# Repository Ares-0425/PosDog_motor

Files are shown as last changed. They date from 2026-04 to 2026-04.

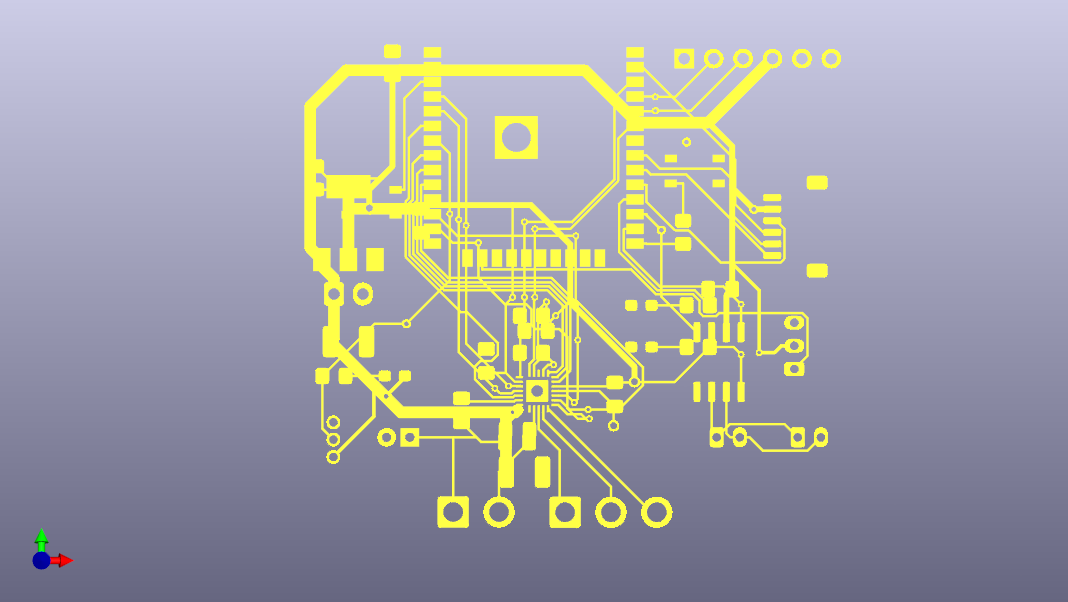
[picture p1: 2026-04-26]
drv8311/drv8311.png

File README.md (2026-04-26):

# PosDog_motor
四脚歩行ロボット「PosDog」のモータードライバプログラムと回路CADデータのレポジトリ
## 動作環境
プログラムはVSCode＋PlatformIO環境で作成しています。
回路CADはKiCADを使用し、JLCPCBでの発注を想定しています。
## ファイル
### プログラム
レポジトリ全体がPlatformIOのプログラムフォルダになっていますが、いじるべきプログラムは"src"フォルダ内に入っています。
- main.cpp  
  メインプログラムファイル。主にSimpleFOC（モーター制御ライブラリ）の設定、SimpleFOC制御ループ、CAN通信で取得した文字列の識別と文字列に応じた動作の実行、キャリブレーション動作の定義、を行っている。
- can.hpp  
  can.cppのヘッダー
- can.cpp  
  can通信用ファイル。設定と受信時のID及び文字列格納。
- dob.hpp  
  dob.cppのヘッダー
- dob.cpp  
  外乱オブザーバーと、外乱オブザーバーを考慮したトルク制御と角度制御の指令値出力。
- identification.hpp  
  identification.cppのヘッダー
- identification.cpp  
  システム同定を一瞬やろうとした時の残骸
### 回路
"drv8311"フォルダ内に入っています。
- drv8311.kicad_pro  
  kicadプロジェクトファイル
- drv8311.kicad_sch  
  kicad回路図ファイル
- drv8311.kicad_pcb  
  kicadPCBファイル
- production
  - drv8311.zip  
    JLCPCB発注用ファイル
## 基本の使いかた
プログラムを書き込む脚に合わせて、main.cppの"#define LEG"の数字を変更する。

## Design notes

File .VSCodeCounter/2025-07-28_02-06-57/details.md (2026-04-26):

# Details

Date : 2025-07-28 02:06:57

Directory e:\\OneDrive\\vscode\\zyudou\\M5-controll

Total : 17 files,  1201 codes, 63 comments, 196 blanks, all 1460 lines

[Summary](results.md) / Details / [Diff Summary](diff.md) / [Diff Details](diff-details.md)

## Files
| filename | language | code | comment | blank | total |
| :--- | :--- | ---: | ---: | ---: | ---: |
| [M5-controll/.VSCodeCounter/2025-07-28\_02-06-30/details.md](/M5-controll/.VSCodeCounter/2025-07-28_02-06-30/details.md) | Markdown | 21 | 0 | 6 | 27 |
| [M5-controll/.VSCodeCounter/2025-07-28\_02-06-30/diff-details.md](/M5-controll/.VSCodeCounter/2025-07-28_02-06-30/diff-details.md) | Markdown | 9 | 0 | 6 | 15 |
| [M5-controll/.VSCodeCounter/2025-07-28\_02-06-30/diff.md](/M5-controll/.VSCodeCounter/2025-07-28_02-06-30/diff.md) | Markdown | 12 | 0 | 7 | 19 |
| [M5-controll/.VSCodeCounter/2025-07-28\_02-06-30/results.json](/M5-controll/.VSCodeCounter/2025-07-28_02-06-30/results.json) | JSON | 1 | 0 | 0 | 1 |
| [M5-controll/.VSCodeCounter/2025-07-28\_02-06-30/results.md](/M5-controll/.VSCodeCounter/2025-07-28_02-06-30/results.md) | Markdown | 17 | 0 | 7 | 24 |
| [M5-controll/platformio.ini](/M5-controll/platformio.ini) | Ini | 21 | 9 | 5 | 35 |
| [M5-controll/src/can.cpp](/M5-controll/src/can.cpp) | C++ | 59 | 6 | 12 | 77 |
| [M5-controll/src/can.hpp](/M5-controll/src/can.hpp) | C++ | 26 | 2 | 5 | 33 |
| [M5-controll/src/control.cpp](/M5-controll/src/control.cpp) | C++ | 803 | 28 | 98 | 929 |
| [M5-controll/src/control.hpp](/M5-controll/src/control.hpp) | C++ | 19 | 2 | 4 | 25 |
| [M5-controll/src/display.cpp](/M5-controll/src/display.cpp) | C++ | 45 | 0 | 6 | 51 |
| [M5-controll/src/display.hpp](/M5-controll/src/display.hpp) | C++ | 11 | 2 | 5 | 18 |
| [M5-controll/src/imu.cpp](/M5-controll/src/imu.cpp) | C++ | 68 | 14 | 23 | 105 |
| [M5-controll/src/imu.hpp](/M5-controll/src/imu.hpp) | C++ | 13 | 0 | 3 | 16 |
| [M5-controll/src/main.cpp](/M5-controll/src/main.cpp) | C++ | 73 | 0 | 7 | 80 |
| [M5-controll/src/sd.cpp](/M5-controll/src/sd.cpp) | C++ | 0 | 0 | 1 | 1 |
| [M5-controll/src/sd.hpp](/M5-controll/src/sd.hpp) | C++ | 3 | 0 | 1 | 4 |

[Summary](results.md) / Details / [Diff Summary](diff.md) / [Diff Details](diff-details.md)

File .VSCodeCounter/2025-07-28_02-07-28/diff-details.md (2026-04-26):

# Diff Details

Date : 2025-07-28 02:07:28

Directory e:\\OneDrive\\vscode\\zyudou\\simpleFOC_CAN_DOB

Total : 28 files,  -482 codes, 169 comments, -19 blanks, all -332 lines

[Summary](results.md) / [Details](details.md) / [Diff Summary](diff.md) / Diff Details

## Files
| filename | language | code | comment | blank | total |
| :--- | :--- | ---: | ---: | ---: | ---: |
| [M5-controll/.VSCodeCounter/2025-07-28\_02-06-30/details.md](/M5-controll/.VSCodeCounter/2025-07-28_02-06-30/details.md) | Markdown | -21 | 0 | -6 | -27 |
| [M5-controll/.VSCodeCounter/2025-07-28\_02-06-30/diff-details.md](/M5-controll/.VSCodeCounter/2025-07-28_02-06-30/diff-details.md) | Markdown | -9 | 0 | -6 | -15 |
| [M5-controll/.VSCodeCounter/2025-07-28\_02-06-30/diff.md](/M5-controll/.VSCodeCounter/2025-07-28_02-06-30/diff.md) | Markdown | -12 | 0 | -7 | -19 |
| [M5-controll/.VSCodeCounter/2025-07-28\_02-06-30/results.json](/M5-controll/.VSCodeCounter/2025-07-28_02-06-30/results.json) | JSON | -1 | 0 | 0 | -1 |
| [M5-controll/.VSCodeCounter/2025-07-28\_02-06-30/results.md](/M5-controll/.VSCodeCounter/2025-07-28_02-06-30/results.md) | Markdown | -17 | 0 | -7 | -24 |
| [M5-controll/platformio.ini](/M5-controll/platformio.ini) | Ini | -21 | -9 | -5 | -35 |
| [M5-controll/src/can.cpp](/M5-controll/src/can.cpp) | C++ | -59 | -6 | -12 | -77 |
| [M5-controll/src/can.hpp](/M5-controll/src/can.hpp) | C++ | -26 | -2 | -5 | -33 |
| [M5-controll/src/control.cpp](/M5-controll/src/control.cpp) | C++ | -803 | -28 | -98 | -929 |
| [M5-controll/src/control.hpp](/M5-controll/src/control.hpp) | C++ | -19 | -2 | -4 | -25 |
| [M5-controll/src/display.cpp](/M5-controll/src/display.cpp) | C++ | -45 | 0 | -6 | -51 |
| [M5-controll/src/display.hpp](/M5-controll/src/display.hpp) | C++ | -11 | -2 | -5 | -18 |
| [M5-controll/src/imu.cpp](/M5-controll/src/imu.cpp) | C++ | -68 | -14 | -23 | -105 |
| [M5-controll/src/imu.hpp](/M5-controll/src/imu.hpp) | C++ | -13 | 0 | -3 | -16 |
| [M5-controll/src/main.cpp](/M5-controll/src/main.cpp) | C++ | -73 | 0 | -7 | -80 |
| [M5-controll/src/sd.cpp](/M5-controll/src/sd.cpp) | C++ | 0 | 0 | -1 | -1 |
| [M5-controll/src/sd.hpp](/M5-controll/src/sd.hpp) | C++ | -3 | 0 | -1 | -4 |
| [simpleFOC\_CAN\_DOB/.VSCodeCounter/2025-07-28\_02-06-57/details.md](/simpleFOC_CAN_DOB/.VSCodeCounter/2025-07-28_02-06-57/details.md) | Markdown | 26 | 0 | 6 | 32 |
| [simpleFOC\_CAN\_DOB/.VSCodeCounter/2025-07-28\_02-06-57/diff-details.md](/simpleFOC_CAN_DOB/.VSCodeCounter/2025-07-28_02-06-57/diff-details.md) | Markdown | 9 | 0 | 6 | 15 |
| [simpleFOC\_CAN\_DOB/.VSCodeCounter/2025-07-28\_02-06-57/diff.md](/simpleFOC_CAN_DOB/.VSCodeCounter/2025-07-28_02-06-57/diff.md) | Markdown | 12 | 0 | 7 | 19 |
| [simpleFOC\_CAN\_DOB/.VSCodeCounter/2025-07-28\_02-06-57/results.json](/simpleFOC_CAN_DOB/.VSCodeCounter/2025-07-28_02-06-57/results.json) | JSON | 1 | 0 | 0 | 1 |
| [simpleFOC\_CAN\_DOB/.VSCodeCounter/2025-07-28\_02-06-57/results.md](/simpleFOC_CAN_DOB/.VSCodeCounter/2025-07-28_02-06-57/results.md) | Markdown | 21 | 0 | 7 | 28 |
| [simpleFOC\_CAN\_DOB/platformio.ini](/simpleFOC_CAN_DOB/platformio.ini) | Ini | 12 | 9 | 2 | 23 |
| [simpleFOC\_CAN\_DOB/src/can.cpp](/simpleFOC_CAN_DOB/src/can.cpp) | C++ | 62 | 4 | 14 | 80 |
| [simpleFOC\_CAN\_DOB/src/can.hpp](/simpleFOC_CAN_DOB/src/can.hpp) | C++ | 17 | 2 | 5 | 24 |
| [simpleFOC\_CAN\_DOB/src/dob.cpp](/simpleFOC_CAN_DOB/src/dob.cpp) | C++ | 118 | 51 | 38 | 207 |
| [simpleFOC\_CAN\_DOB/src/dob.hpp](/simpleFOC_CAN_DOB/src/dob.hpp) | C++ | 41 | 7 | 10 | 58 |
| [simpleFOC\_CAN\_DOB/src/main.cpp](/simpleFOC_CAN_DOB/src/main.cpp) | C++ | 400 | 159 | 82 | 641 |

[Summary](results.md) / [Details](details.md) / [Diff Summary](diff.md) / Diff Details

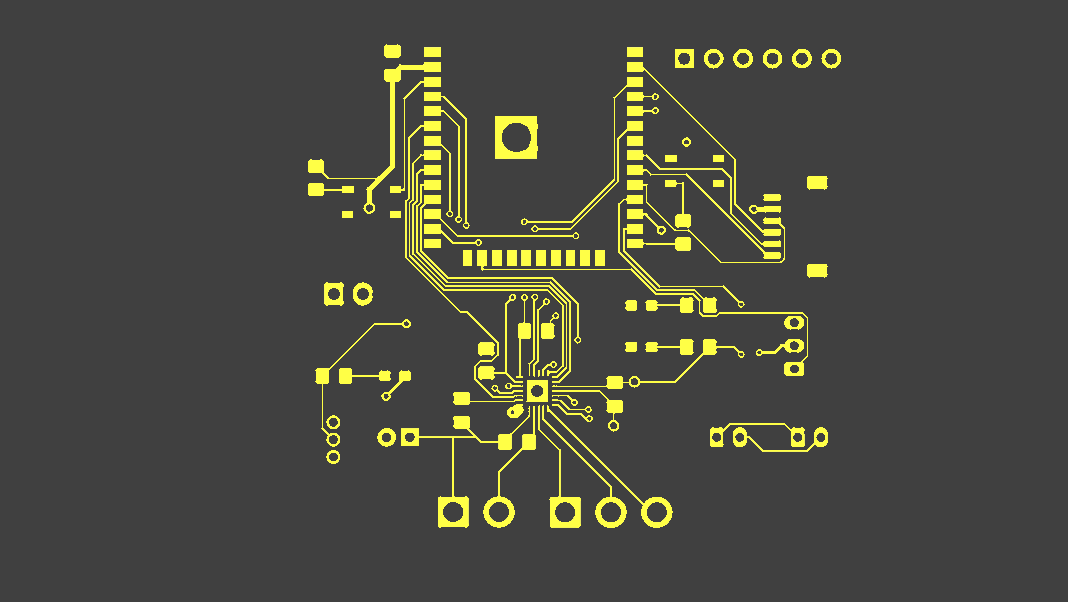
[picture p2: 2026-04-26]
drv8311/drv8311-1.png

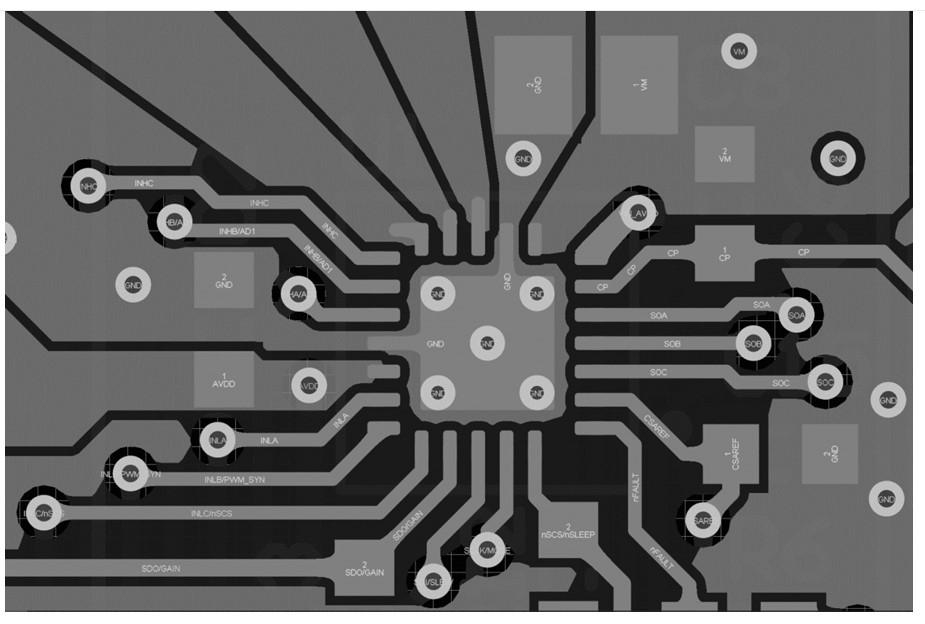
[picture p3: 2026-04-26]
drv8311/スクリーンショット 2024-01-09 131917.jpg

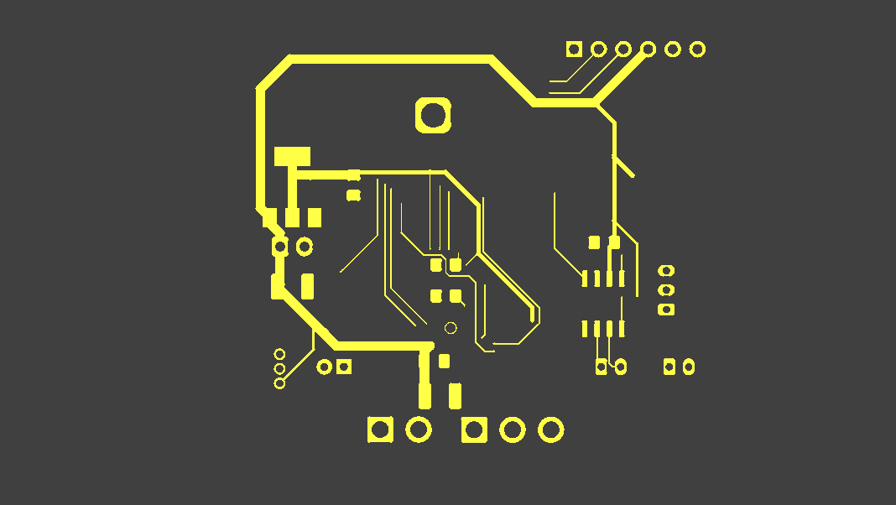
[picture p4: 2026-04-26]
drv8311/drv8311-2.png

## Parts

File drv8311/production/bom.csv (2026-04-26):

Designator | Footprint | Quantity | Value | LCSC Part #
BOOT1, RESET1 | SW_Push_1P1T_NO_Vertical_Wuerth_434133025816 | 2 | SW_Push
C1 | 0805 | 1 | 1u
C10, C12, C2, C3, C4, C8 | 0805 | 6 | 0.1u
C5 | CP_Radial_D5.0mm_P2.00mm | 1 | 10u
C6, C9 | 1210 | 2 | 10u
C7 | 0805 | 1 | 22u
J1 | JST_VH_B3P-VH_1x03_P3.96mm_Vertical | 1 | VH_3B
J10 | JST_ZH_S03B | 1 | ZH_3B
J2 | JST_SH_SM06B-SRSS-TB_1x06-1MP_P1.00mm_Horizontal | 1 | SH_6B
J3 | PinHeader_1x06_P2.54mm_Vertical | 1 | Conn_01x06_Pin
J5 | JST_XH_B2B-XH-A_1x02_P2.50mm_Vertical | 1 | XH_2B
J6 | JST_VH_B2P-VH_1x02_P3.96mm_Vertical | 1 | ZH_2B
J7, J8 | JST_PH_B2B-PH-K_1x02_P2.00mm_Vertical | 2 | PH_2B
J9 | JST_PH_B3B-PH-K_1x03_P2.00mm_Vertical | 1 | PH_3B
PHOTO1 | 0603 | 1 | LED
POWER1 | 0603 | 1 | OSHR1608
R1, R4 | 0805 | 2 | 47k
R2 | 0805 | 1 | 5.1k
R3, R5 | 0805 | 2 | 10k
R7 | 0805 | 1 | 220
R8 | 0805 | 1 | 75
R9 | 0805 | 1 | 540
STATUS1 | 0603 | 1 | OSYG1608
U1 | WQFN-24-1EP_4x4mm_P0.5mm_EP2.45x2.45mm | 1 | DRV8311HRRWR
U2 | ESP32-WROOM-32UE | 1 | ESP32-WROOM-E
U3 | SO-8_3.9x4.9mm_P1.27mm | 1 | TJA1441AT
U4 | SOT-223-3_TabPin2 | 1 | AZ1117-3.3

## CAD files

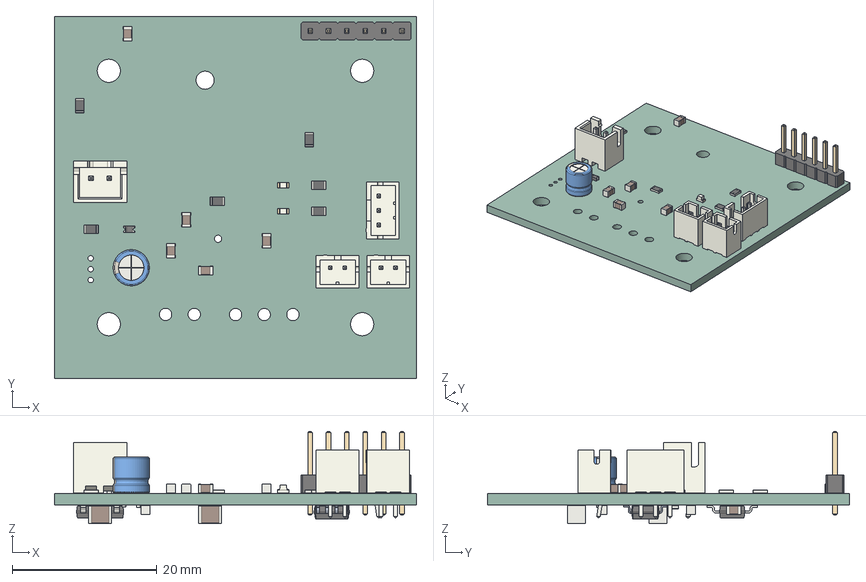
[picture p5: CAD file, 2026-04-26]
drv8311/drv8311.step
50.0 x 50.0 x 12.7 mm
R_0805_2012Metric x 8
D_0603
C_0805_2012Metric x 8
PinHeader_1x06_P254mm_Vertical
LED_0603_1608Metric x 2
JST_B2B_PH_K x 2
JST_B3B_PH_K
CP_Radial_D50mm_P200mm
JST_B2B_XH_A
SOT_223
C_1210_3225Metric x 2
CQ assembly
drv8311_PCB

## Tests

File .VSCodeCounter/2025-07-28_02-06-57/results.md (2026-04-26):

# Summary

Date : 2025-07-28 02:06:57

Directory e:\\OneDrive\\vscode\\zyudou\\M5-controll

Total : 17 files,  1201 codes, 63 comments, 196 blanks, all 1460 lines

Summary / [Details](details.md) / [Diff Summary](diff.md) / [Diff Details](diff-details.md)

## Languages
| language | files | code | comment | blank | total |
| :--- | ---: | ---: | ---: | ---: | ---: |
| C++ | 11 | 1,120 | 54 | 165 | 1,339 |
| Markdown | 4 | 59 | 0 | 26 | 85 |
| Ini | 1 | 21 | 9 | 5 | 35 |
| JSON | 1 | 1 | 0 | 0 | 1 |

## Directories
| path | files | code | comment | blank | total |
| :--- | ---: | ---: | ---: | ---: | ---: |
| . | 17 | 1,201 | 63 | 196 | 1,460 |
| . (Files) | 1 | 21 | 9 | 5 | 35 |
| .VSCodeCounter | 5 | 60 | 0 | 26 | 86 |
| .VSCodeCounter\\2025-07-28_02-06-30 | 5 | 60 | 0 | 26 | 86 |
| src | 11 | 1,120 | 54 | 165 | 1,339 |

Summary / [Details](details.md) / [Diff Summary](diff.md) / [Diff Details](diff-details.md)

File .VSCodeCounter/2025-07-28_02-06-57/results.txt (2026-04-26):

Date : 2025-07-28 02:06:57
Directory : e:\OneDrive\vscode\zyudou\M5-controll
Total : 17 files,  1201 codes, 63 comments, 196 blanks, all 1460 lines

Languages
+----------+------------+------------+------------+------------+------------+
| language | files      | code       | comment    | blank      | total      |
+----------+------------+------------+------------+------------+------------+
| C++      |         11 |      1,120 |         54 |        165 |      1,339 |
| Markdown |          4 |         59 |          0 |         26 |         85 |
| Ini      |          1 |         21 |          9 |          5 |         35 |
| JSON     |          1 |          1 |          0 |          0 |          1 |
+----------+------------+------------+------------+------------+------------+

Directories
+------------------------------------------------------------------------------------------+------------+------------+------------+------------+------------+
| path                                                                                     | files      | code       | comment    | blank      | total      |
+------------------------------------------------------------------------------------------+------------+------------+------------+------------+------------+
| .                                                                                        |         17 |      1,201 |         63 |        196 |      1,460 |
| . (Files)                                                                                |          1 |         21 |          9 |          5 |         35 |
| .VSCodeCounter                                                                           |          5 |         60 |          0 |         26 |         86 |
| .VSCodeCounter\2025-07-28_02-06-30                                                       |          5 |         60 |          0 |         26 |         86 |
| src                                                                                      |         11 |      1,120 |         54 |        165 |      1,339 |
+------------------------------------------------------------------------------------------+------------+------------+------------+------------+------------+

Files
+------------------------------------------------------------------------------------------+----------+------------+------------+------------+------------+
| filename                                                                                 | language | code       | comment    | blank      | total      |
+------------------------------------------------------------------------------------------+----------+------------+------------+------------+------------+
| e:\OneDrive\vscode\zyudou\M5-controll\.VSCodeCounter\2025-07-28_02-06-30\details.md      | Markdown |         21 |          0 |          6 |         27 |
| e:\OneDrive\vscode\zyudou\M5-controll\.VSCodeCounter\2025-07-28_02-06-30\diff-details.md | Markdown |          9 |          0 |          6 |         15 |
| e:\OneDrive\vscode\zyudou\M5-controll\.VSCodeCounter\2025-07-28_02-06-30\diff.md         | Markdown |         12 |          0 |          7 |         19 |
| e:\OneDrive\vscode\zyudou\M5-controll\.VSCodeCounter\2025-07-28_02-06-30\results.json    | JSON     |          1 |          0 |          0 |          1 |
| e:\OneDrive\vscode\zyudou\M5-controll\.VSCodeCounter\2025-07-28_02-06-30\results.md      | Markdown |         17 |          0 |          7 |         24 |
| e:\OneDrive\vscode\zyudou\M5-controll\platformio.ini                                     | Ini      |         21 |          9 |          5 |         35 |
| e:\OneDrive\vscode\zyudou\M5-controll\src\can.cpp                                        | C++      |         59 |          6 |         12 |         77 |
| e:\OneDrive\vscode\zyudou\M5-controll\src\can.hpp                                        | C++      |         26 |          2 |          5 |         33 |
| e:\OneDrive\vscode\zyudou\M5-controll\src\control.cpp                                    | C++      |        803 |         28 |         98 |        929 |
| e:\OneDrive\vscode\zyudou\M5-controll\src\control.hpp                                    | C++      |         19 |          2 |          4 |         25 |
| e:\OneDrive\vscode\zyudou\M5-controll\src\display.cpp                                    | C++      |         45 |          0 |          6 |         51 |
| e:\OneDrive\vscode\zyudou\M5-controll\src\display.hpp                                    | C++      |         11 |          2 |          5 |         18 |
| e:\OneDrive\vscode\zyudou\M5-controll\src\imu.cpp                                        | C++      |         68 |         14 |         23 |        105 |
| e:\OneDrive\vscode\zyudou\M5-controll\src\imu.hpp                                        | C++      |         13 |          0 |          3 |         16 |
| e:\OneDrive\vscode\zyudou\M5-controll\src\main.cpp                                       | C++      |         73 |          0 |          7 |         80 |
| e:\OneDrive\vscode\zyudou\M5-controll\src\sd.cpp                                         | C++      |          0 |          0 |          1 |          1 |
| e:\OneDrive\vscode\zyudou\M5-controll\src\sd.hpp                                         | C++      |          3 |          0 |          1 |          4 |
| Total                                                                                    |          |      1,201 |         63 |        196 |      1,460 |
+------------------------------------------------------------------------------------------+----------+------------+------------+------------+------------+

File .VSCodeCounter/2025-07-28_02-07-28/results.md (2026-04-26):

# Summary

Date : 2025-07-28 02:07:28

Directory e:\\OneDrive\\vscode\\zyudou\\simpleFOC_CAN_DOB

Total : 11 files,  719 codes, 232 comments, 177 blanks, all 1128 lines

Summary / [Details](details.md) / [Diff Summary](diff.md) / [Diff Details](diff-details.md)

## Languages
| language | files | code | comment | blank | total |
| :--- | ---: | ---: | ---: | ---: | ---: |
| C++ | 5 | 638 | 223 | 149 | 1,010 |
| Markdown | 4 | 68 | 0 | 26 | 94 |
| Ini | 1 | 12 | 9 | 2 | 23 |
| JSON | 1 | 1 | 0 | 0 | 1 |

## Directories
| path | files | code | comment | blank | total |
| :--- | ---: | ---: | ---: | ---: | ---: |
| . | 11 | 719 | 232 | 177 | 1,128 |
| . (Files) | 1 | 12 | 9 | 2 | 23 |
| .VSCodeCounter | 5 | 69 | 0 | 26 | 95 |
| .VSCodeCounter\\2025-07-28_02-06-57 | 5 | 69 | 0 | 26 | 95 |
| src | 5 | 638 | 223 | 149 | 1,010 |

Summary / [Details](details.md) / [Diff Summary](diff.md) / [Diff Details](diff-details.md)

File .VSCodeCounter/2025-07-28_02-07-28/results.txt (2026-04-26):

Date : 2025-07-28 02:07:28
Directory : e:\OneDrive\vscode\zyudou\simpleFOC_CAN_DOB
Total : 11 files,  719 codes, 232 comments, 177 blanks, all 1128 lines

Languages
+----------+------------+------------+------------+------------+------------+
| language | files      | code       | comment    | blank      | total      |
+----------+------------+------------+------------+------------+------------+
| C++      |          5 |        638 |        223 |        149 |      1,010 |
| Markdown |          4 |         68 |          0 |         26 |         94 |
| Ini      |          1 |         12 |          9 |          2 |         23 |
| JSON     |          1 |          1 |          0 |          0 |          1 |
+----------+------------+------------+------------+------------+------------+

Directories
+------------------------------------------------------------------------------------------------+------------+------------+------------+------------+------------+
| path                                                                                           | files      | code       | comment    | blank      | total      |
+------------------------------------------------------------------------------------------------+------------+------------+------------+------------+------------+
| .                                                                                              |         11 |        719 |        232 |        177 |      1,128 |
| . (Files)                                                                                      |          1 |         12 |          9 |          2 |         23 |
| .VSCodeCounter                                                                                 |          5 |         69 |          0 |         26 |         95 |
| .VSCodeCounter\2025-07-28_02-06-57                                                             |          5 |         69 |          0 |         26 |         95 |
| src                                                                                            |          5 |        638 |        223 |        149 |      1,010 |
+------------------------------------------------------------------------------------------------+------------+------------+------------+------------+------------+

Files
+------------------------------------------------------------------------------------------------+----------+------------+------------+------------+------------+
| filename                                                                                       | language | code       | comment    | blank      | total      |
+------------------------------------------------------------------------------------------------+----------+------------+------------+------------+------------+
| e:\OneDrive\vscode\zyudou\simpleFOC_CAN_DOB\.VSCodeCounter\2025-07-28_02-06-57\details.md      | Markdown |         26 |          0 |          6 |         32 |
| e:\OneDrive\vscode\zyudou\simpleFOC_CAN_DOB\.VSCodeCounter\2025-07-28_02-06-57\diff-details.md | Markdown |          9 |          0 |          6 |         15 |
| e:\OneDrive\vscode\zyudou\simpleFOC_CAN_DOB\.VSCodeCounter\2025-07-28_02-06-57\diff.md         | Markdown |         12 |          0 |          7 |         19 |
| e:\OneDrive\vscode\zyudou\simpleFOC_CAN_DOB\.VSCodeCounter\2025-07-28_02-06-57\results.json    | JSON     |          1 |          0 |          0 |          1 |
| e:\OneDrive\vscode\zyudou\simpleFOC_CAN_DOB\.VSCodeCounter\2025-07-28_02-06-57\results.md      | Markdown |         21 |          0 |          7 |         28 |
| e:\OneDrive\vscode\zyudou\simpleFOC_CAN_DOB\platformio.ini                                     | Ini      |         12 |          9 |          2 |         23 |
| e:\OneDrive\vscode\zyudou\simpleFOC_CAN_DOB\src\can.cpp                                        | C++      |         62 |          4 |         14 |         80 |
| e:\OneDrive\vscode\zyudou\simpleFOC_CAN_DOB\src\can.hpp                                        | C++      |         17 |          2 |          5 |         24 |
| e:\OneDrive\vscode\zyudou\simpleFOC_CAN_DOB\src\dob.cpp                                        | C++      |        118 |         51 |         38 |        207 |
| e:\OneDrive\vscode\zyudou\simpleFOC_CAN_DOB\src\dob.hpp                                        | C++      |         41 |          7 |         10 |         58 |
| e:\OneDrive\vscode\zyudou\simpleFOC_CAN_DOB\src\main.cpp                                       | C++      |        400 |        159 |         82 |        641 |
| Total                                                                                          |          |        719 |        232 |        177 |      1,128 |
+------------------------------------------------------------------------------------------------+----------+------------+------------+------------+------------+

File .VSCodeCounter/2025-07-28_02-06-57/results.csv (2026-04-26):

filename | "language" | "Ini" | "C++" | "Markdown" | "JSON" | "comment" | "blank" | "total"
e:\OneDrive\vscode\zyudou\M5-controll\.VSCodeCounter\2025-07-28_02-06-30\details.md | "Markdown" | 0 | 0 | 21 | 0 | 0 | 6 | 27
e:\OneDrive\vscode\zyudou\M5-controll\.VSCodeCounter\2025-07-28_02-06-30\diff-details.md | "Markdown" | 0 | 0 | 9 | 0 | 0 | 6 | 15
e:\OneDrive\vscode\zyudou\M5-controll\.VSCodeCounter\2025-07-28_02-06-30\diff.md | "Markdown" | 0 | 0 | 12 | 0 | 0 | 7 | 19
e:\OneDrive\vscode\zyudou\M5-controll\.VSCodeCounter\2025-07-28_02-06-30\results.json | "JSON" | 0 | 0 | 0 | 1 | 0 | 0 | 1
e:\OneDrive\vscode\zyudou\M5-controll\.VSCodeCounter\2025-07-28_02-06-30\results.md | "Markdown" | 0 | 0 | 17 | 0 | 0 | 7 | 24
e:\OneDrive\vscode\zyudou\M5-controll\platformio.ini | "Ini" | 21 | 0 | 0 | 0 | 9 | 5 | 35
e:\OneDrive\vscode\zyudou\M5-controll\src\can.cpp | "C++" | 0 | 59 | 0 | 0 | 6 | 12 | 77
e:\OneDrive\vscode\zyudou\M5-controll\src\can.hpp | "C++" | 0 | 26 | 0 | 0 | 2 | 5 | 33
e:\OneDrive\vscode\zyudou\M5-controll\src\control.cpp | "C++" | 0 | 803 | 0 | 0 | 28 | 98 | 929
e:\OneDrive\vscode\zyudou\M5-controll\src\control.hpp | "C++" | 0 | 19 | 0 | 0 | 2 | 4 | 25
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

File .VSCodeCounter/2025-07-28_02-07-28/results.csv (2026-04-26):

filename | "language" | "C++" | "Ini" | "Markdown" | "JSON" | "comment" | "blank" | "total"
e:\OneDrive\vscode\zyudou\simpleFOC_CAN_DOB\.VSCodeCounter\2025-07-28_02-06-57\details.md | "Markdown" | 0 | 0 | 26 | 0 | 0 | 6 | 32
e:\OneDrive\vscode\zyudou\simpleFOC_CAN_DOB\.VSCodeCounter\2025-07-28_02-06-57\diff-details.md | "Markdown" | 0 | 0 | 9 | 0 | 0 | 6 | 15
e:\OneDrive\vscode\zyudou\simpleFOC_CAN_DOB\.VSCodeCounter\2025-07-28_02-06-57\diff.md | "Markdown" | 0 | 0 | 12 | 0 | 0 | 7 | 19
e:\OneDrive\vscode\zyudou\simpleFOC_CAN_DOB\.VSCodeCounter\2025-07-28_02-06-57\results.json | "JSON" | 0 | 0 | 0 | 1 | 0 | 0 | 1
e:\OneDrive\vscode\zyudou\simpleFOC_CAN_DOB\.VSCodeCounter\2025-07-28_02-06-57\results.md | "Markdown" | 0 | 0 | 21 | 0 | 0 | 7 | 28
e:\OneDrive\vscode\zyudou\simpleFOC_CAN_DOB\platformio.ini | "Ini" | 0 | 12 | 0 | 0 | 9 | 2 | 23
e:\OneDrive\vscode\zyudou\simpleFOC_CAN_DOB\src\can.cpp | "C++" | 62 | 0 | 0 | 0 | 4 | 14 | 80
e:\OneDrive\vscode\zyudou\simpleFOC_CAN_DOB\src\can.hpp | "C++" | 17 | 0 | 0 | 0 | 2 | 5 | 24
e:\OneDrive\vscode\zyudou\simpleFOC_CAN_DOB\src\dob.cpp | "C++" | 118 | 0 | 0 | 0 | 51 | 38 | 207
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

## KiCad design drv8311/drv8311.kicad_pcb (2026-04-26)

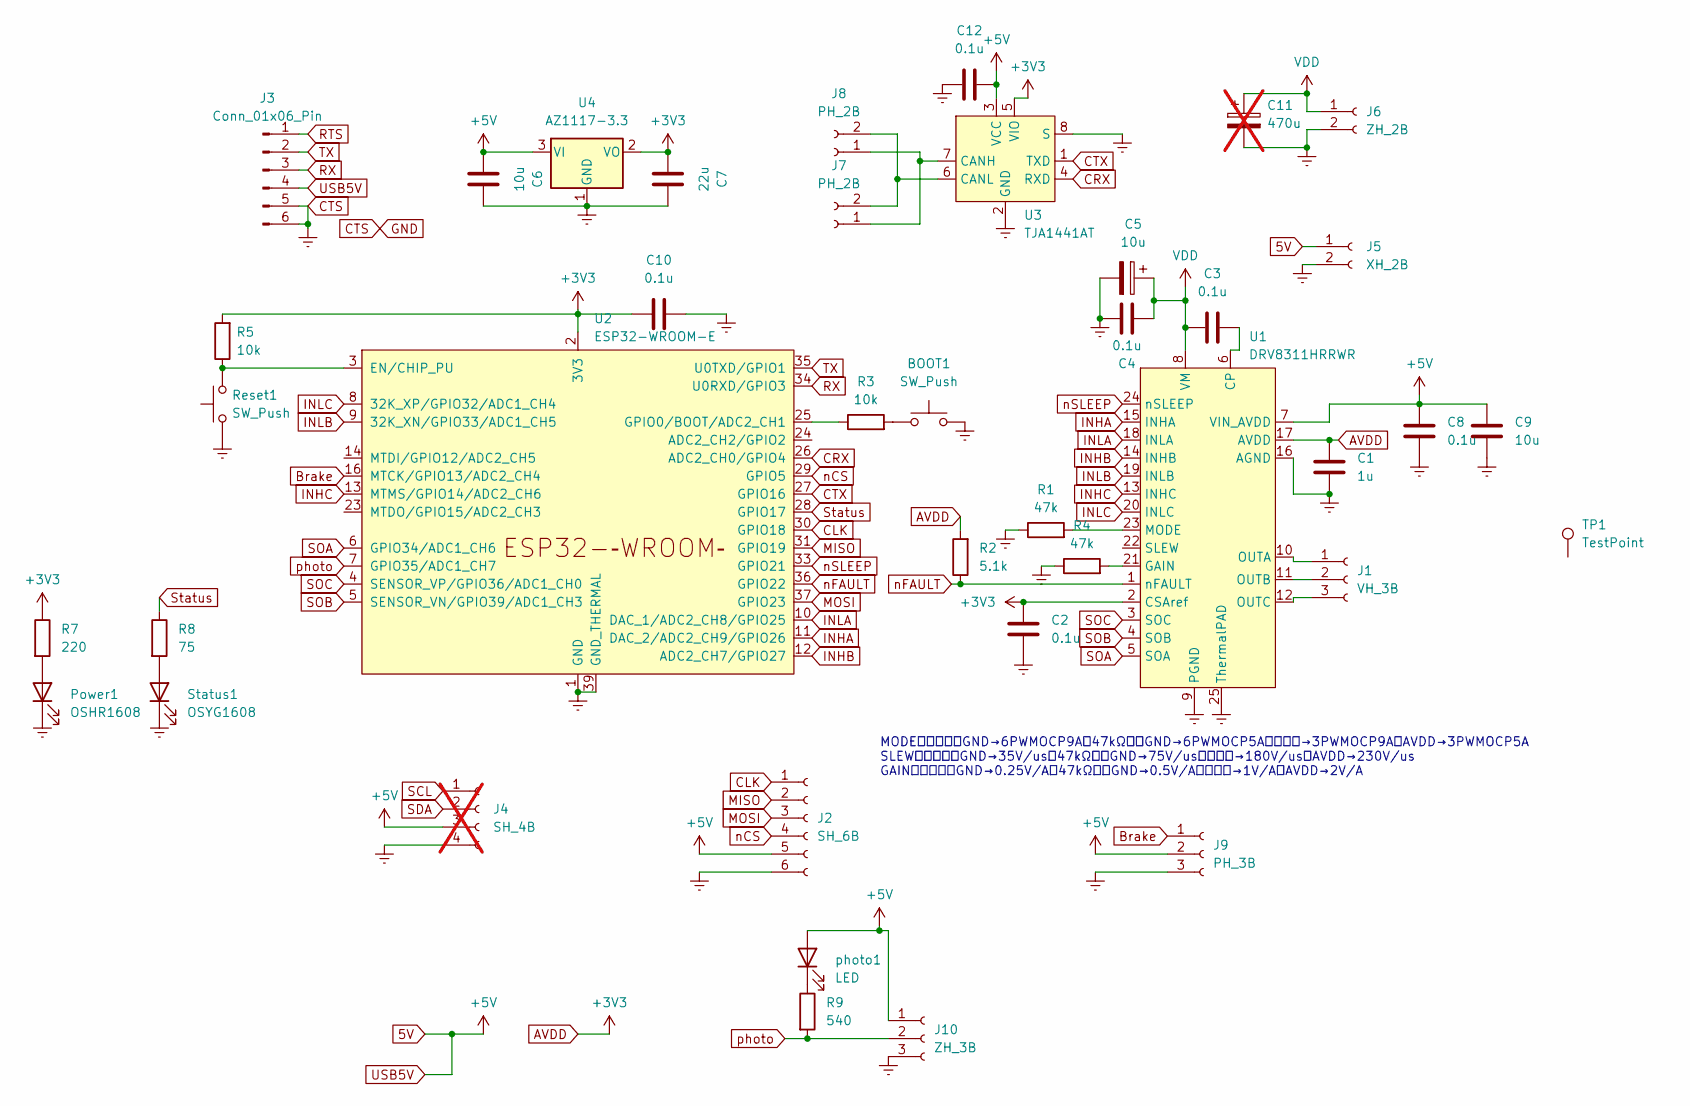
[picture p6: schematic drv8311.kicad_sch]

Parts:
BOOT1: SW_Push; SW_Push_1P1T_NO_Vertical_Wuerth_434133025816
C1: 1u; C_0805_2012Metric_Pad1.18x1.45mm_HandSolder
C2, C3, C4, C8, C10, C12: 0.1u; C_0805_2012Metric_Pad1.18x1.45mm_HandSolder
C5: 10u; CP_Radial_D5.0mm_P2.00mm
C6, C9: 10u; C_1210_3225Metric_Pad1.33x2.70mm_HandSolder
C7: 22u; C_0805_2012Metric_Pad1.18x1.45mm_HandSolder
C11: 470u; not fitted
J1: VH_3B; JST_VH_B3P-VH_1x03_P3.96mm_Vertical
J2: SH_6B; JST_SH_SM06B-SRSS-TB_1x06-1MP_P1.00mm_Horizontal
J3: Conn_01x06_Pin; PinHeader_1x06_P2.54mm_Vertical
J4: SH_4B; JST_SH_SM04B-SRSS-TB_1x04-1MP_P1.00mm_Horizontal; not fitted
J5: XH_2B; JST_XH_B2B-XH-A_1x02_P2.50mm_Vertical
J6: ZH_2B; JST_VH_B2P-VH_1x02_P3.96mm_Vertical
J7, J8: PH_2B; JST_PH_B2B-PH-K_1x02_P2.00mm_Vertical
J9: PH_3B; JST_PH_B3B-PH-K_1x03_P2.00mm_Vertical
J10: ZH_3B; JST_ZH_S03B
Power1: OSHR1608; LED_0603_1608Metric_Pad1.05x0.95mm_HandSolder
R1, R4: 47k; R_0805_2012Metric_Pad1.20x1.40mm_HandSolder
R2: 5.1k; R_0805_2012Metric_Pad1.20x1.40mm_HandSolder
R3, R5: 10k; R_0805_2012Metric_Pad1.20x1.40mm_HandSolder
R7: 220; R_0805_2012Metric_Pad1.20x1.40mm_HandSolder
R8: 75; R_0805_2012Metric_Pad1.20x1.40mm_HandSolder
R9: 540; R_0805_2012Metric_Pad1.20x1.40mm_HandSolder
Reset1: SW_Push; SW_Push_1P1T_NO_Vertical_Wuerth_434133025816
Status1: OSYG1608; LED_0603_1608Metric_Pad1.05x0.95mm_HandSolder
TP1: TestPoint
U1: DRV8311HRRWR; WQFN-24-1EP_4x4mm_P0.5mm_EP2.45x2.45mm
U2: ESP32-WROOM-E; ESP32-WROOM-32UE
U3: TJA1441AT; SO-8_3.9x4.9mm_P1.27mm
U4: AZ1117-3.3; SOT-223-3_TabPin2
photo1: LED; D_0603_1608Metric_Pad1.05x0.95mm_HandSolder

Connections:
5V: C6.1, C8.1, C9.1, C12.2, J2.5, J3.4, J4.3, J5.1, J9.2, J10.1, U1.7 (VIN_AVDD), U3.3 (VCC), U4.3 (VI), photo1.2 (A)
AVDD: C1.1, C2.1, C7.1, C10.1, R2.2, R5.2, R7.1, U1.2 (CSAref), U1.17 (AVDD), U2.2 (3V3), U3.5 (VIO), U4.2 (VO)
Brake: J9.1, U2.16 (MTCK/GPIO13/ADC2_CH4)
CLK: J2.1, U2.30 (GPIO18)
CRX: U2.26 (ADC2_CH0/GPIO4), U3.4 (RXD)
CTS: BOOT1.2, C1.2, C2.2, C4.2, C5.2, C6.2, C7.2, C8.2, C9.2, C10.2, C11.2, C12.1, J2.6, J3.5, J3.6, J4.4, J5.2, J6.2, J9.3, J10.3, Power1.1 (K), R1.1, R4.1, Reset1.1, Status1.1 (K), U1.9 (PGND), U1.16 (AGND), U1.25 (ThermalPAD), U2.1 (GND), U2.15 (GND), U2.38 (GND), U2.39 (GND_THERMAL), U3.2 (GND), U3.8 (S), U4.1 (GND)
CTX: U2.27 (GPIO16), U3.1 (TXD)
INHA: U1.15 (INHA), U2.11 (DAC_2/ADC2_CH9/GPIO26)
INHB: U1.14 (INHB), U2.12 (ADC2_CH7/GPIO27)
INHC: U1.13 (INHC), U2.13 (MTMS/GPIO14/ADC2_CH6)
INLA: U1.18 (INLA), U2.10 (DAC_1/ADC2_CH8/GPIO25)
INLB: U1.19 (INLB), U2.9 (32K_XN/GPIO33/ADC1_CH5)
INLC: U1.20 (INLC), U2.8 (32K_XP/GPIO32/ADC1_CH4)
MISO: J2.2, U2.31 (GPIO19)
MOSI: J2.3, U2.37 (GPIO23)
unnamed: BOOT1.1, R3.2
unnamed: J1.1, U1.10 (OUTA)
unnamed: J1.2, U1.11 (OUTB)
unnamed: J1.3, U1.12 (OUTC)
unnamed: J7.1, J8.1, U3.7 (CANH)
unnamed: J7.2, J8.2, U3.6 (CANL)
unnamed: Power1.2 (A), R7.2
unnamed: R8.2, Status1.2 (A)
unnamed: C3.2, U1.6 (CP)
unnamed: R4.2, U1.21 (GAIN)
unnamed: R1.2, U1.23 (MODE)
unnamed: R5.1, Reset1.2, U2.3 (EN/CHIP_PU)
unnamed: R3.1, U2.25 (GPIO0/BOOT/ADC2_CH1)
unnamed: R9.1, photo1.1 (K)
RTS: J3.1
RX: J3.3, U2.34 (U0RXD/GPIO3)
SOA: U1.5 (SOA), U2.6 (GPIO34/ADC1_CH6)
SOB: U1.4 (SOB), U2.5 (SENSOR_VN/GPIO39/ADC1_CH3)
SOC: U1.3 (SOC), U2.4 (SENSOR_VP/GPIO36/ADC1_CH0)
Status: R8.1, U2.28 (GPIO17)
TX: J3.2, U2.35 (U0TXD/GPIO1)
VDD: C3.1, C4.1, C5.1, C11.1, J6.1, U1.8 (VM)
nCS: J2.4, U2.29 (GPIO5)
nFAULT: R2.1, U1.1 (nFAULT), U2.36 (GPIO22)
nSLEEP: U1.24 (nSLEEP), U2.33 (GPIO21)
photo: J10.2, R9.2, U2.7 (GPIO35/ADC1_CH7)

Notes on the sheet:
MODE：そのままGND→6PWMOCP9A、47kΩからGND→6PWMOCP5A、未接続→3PWMOCP9A、AVDD→3PWMOCP5A SLEW：そのままGND→35V/us、47kΩからGND→75V/us、未接続→180V/us、AVDD→230V/us GAIN：そのままGND→0.25V/A、47kΩからGND→0.5V/A、未接続→1V/A、AVDD→2V/A

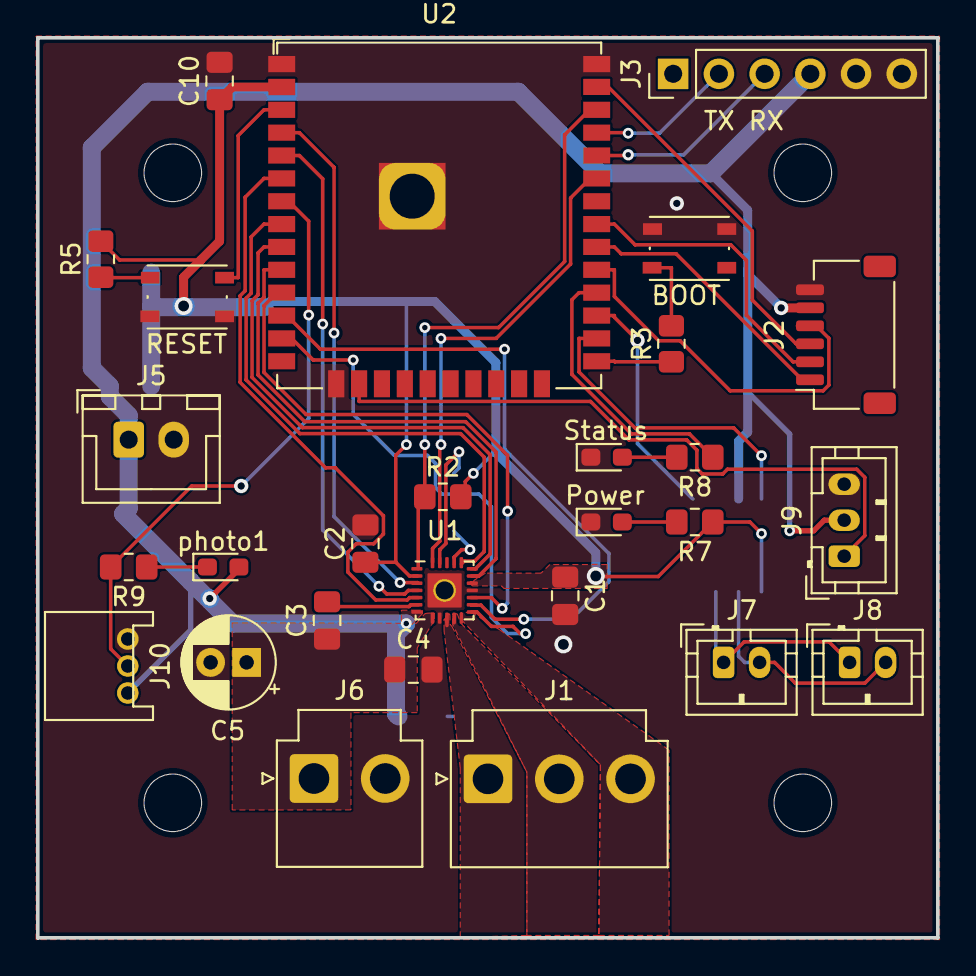
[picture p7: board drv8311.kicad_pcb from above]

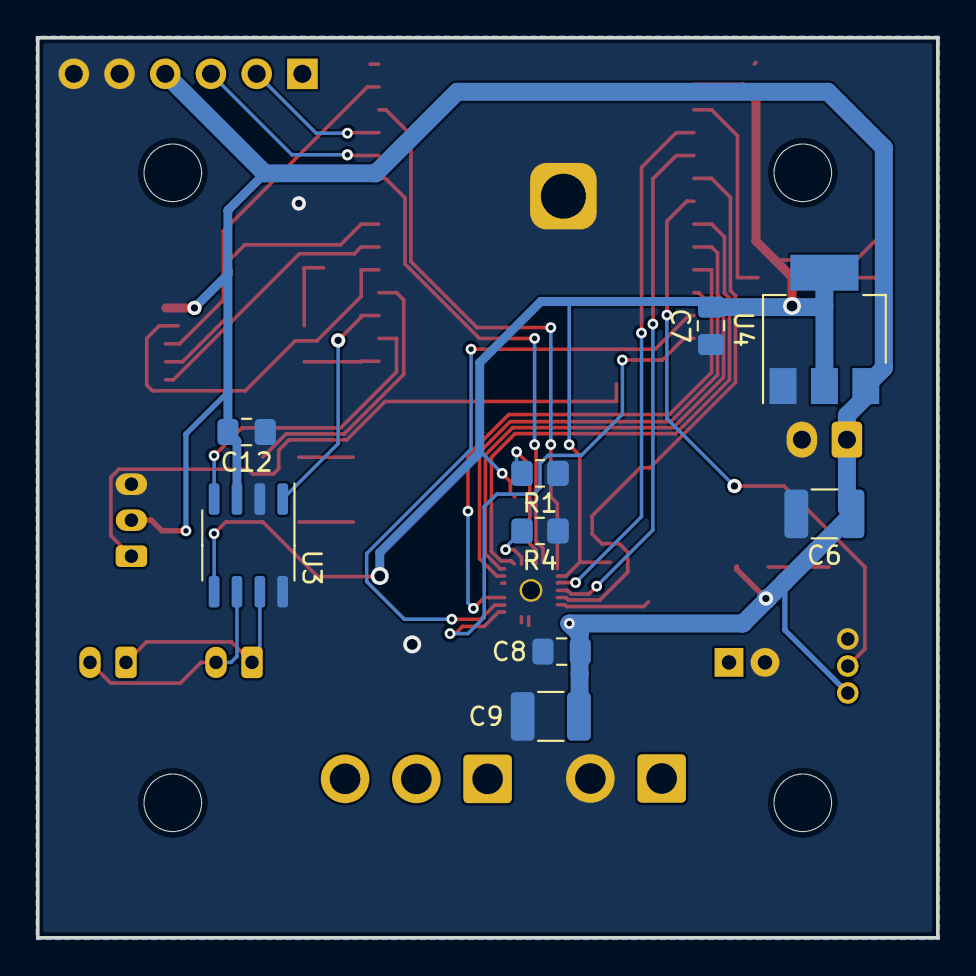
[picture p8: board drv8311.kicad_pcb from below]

Board: 2 copper layers, 50.0 x 50.0 mm, 41 parts (9 on the bottom side), 40 nets.

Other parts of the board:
REF1, REF2, REF3, REF4: MountingHole_3.2mm_M3

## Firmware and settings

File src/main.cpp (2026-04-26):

#include <Arduino.h>
#include <SimpleFOC.h>
//#include <CAN.h>
#include "can.hpp"
#include "dob.hpp"

#define LEG 4  // 1:右前脚, 2:左前脚, 3:右後脚, 4:左後脚

// # SimpleFOC関連
// BLDC motor & driver instance
#define INPUT_VOLTAGE 12 // 電源電圧 [V]

BLDCMotor motor = BLDCMotor(14);
BLDCDriver6PWM driver = BLDCDriver6PWM(26, 25, 27, 33, 14, 32);

// encoder instance
MagneticSensorSPI sensor = MagneticSensorSPI(AS5048_SPI, SS);

//  LowsideCurrentSense(mVpA, adc_a, adc_b, adc_c)
#if (LEG == 1)
  LowsideCurrentSense current_sense = LowsideCurrentSense(500.0, 34, 39, 36);
#elif (LEG == 2)
  LowsideCurrentSense current_sense = LowsideCurrentSense(500.0, 39, 34, 36);
#elif (LEG == 3)
  LowsideCurrentSense current_sense = LowsideCurrentSense(500.0, 39, 34, 36);
#else
  LowsideCurrentSense current_sense = LowsideCurrentSense(500.0, 36, 34, 39);
#endif

// instantiate the commander
Commander command = Commander(Serial,'\n',true);
void doMotor(char* cmd) { command.motor(&motor, cmd); }

void SimpleFOC_setup();

// コントロールモード
#define ANGLEMODE 0
#define VELOCITYMODE 1
#define TORQUEMODE 2
uint8_t control_mode = ANGLEMODE;
boolean is_moving = false; // モーターが動いているかどうか

// 他
float sens_cash = 0.0;  // センサー値の一時保存
float control_cash = 0.0; // コントロール値の一時保存
float control_torque = 0.0;
float torque_cash = 0.0;
float torque_est = 0.0;
float target_torque = 0.0;
float current_limit = 0.5;
float omega;
float alpha;
float current_cash = 0.0; // 電流値の一時保存
float leg_angle;  // 脚の角度(rad)

float sensor_offset = 0.0;
float angle_limit = radians(90.0); // 角度制限(rad)

unsigned long time_now,time_old;
float dt;

#define photo_Pin 35
boolean photo_enable = false; // 光センサーの有効化フラグ
boolean photo_state = false; // 光センサーの状態
boolean photo_old = false; // 光センサーの前回の状態

#define state_Pin 17 // 状態表示用LEDピン

// const int gear_rate = 16;       //ギア比(dobで定義済み)

#if (LEG == 1)
  // 自分のCANID
  #define CAN_ID 0x201
  // 受信するCANID
  #define CAN_MASK 0x101
  // センサーゼロ点
  const float zero_angle = 3.22;
#elif (LEG == 2)
  #define CAN_ID 0x202
  #define CAN_MASK 0x102
  const float zero_angle = 3.44;
#elif (LEG == 3)
  #define CAN_ID 0x203
  #define CAN_MASK 0x103
  const float zero_angle = 0.49;
#else
  #define CAN_ID 0x204
  #define CAN_MASK 0x104
  const float zero_angle = 0.49;
#endif

KalmanEstimator kalman;

TaskHandle_t focTaskHandle = NULL;  // タスクハンドル
void focTask(void *pvParameters);

void CAN_read();

void calibration();
void calibration_2();

void setup() {
  Serial.begin(115200); // シリアル通信速度の設定
  pinMode(photo_Pin, INPUT);
  pinMode(state_Pin, OUTPUT);
  digitalWrite(state_Pin, HIGH);
  
  SimpleFOC_setup();  // SimpleFOCの設定
  motor.disable();
  driver.disable();

  kalman.init();

  CAN_setup(CAN_ID, CAN_MASK);  // CANの設定
  send_CANdata[0] = 'R';
  send_length = 1;
  send_flag = true;

  // Core1にFOC loopタスクを作成
  xTaskCreatePinnedToCore(
    focTask,   // タスク関数
    "FOC",         // タスク名
    4096,             // スタックサイズ
    NULL,             // 引数
    1,                // 優先度
    &focTaskHandle,   // タスクハンドル
    1                 // Core1を指定
  );

  digitalWrite(state_Pin, LOW);
}

int t_count = 0;
void loop() {
  // main FOC algorithm function
  if(receive_flag) {
    // CANメッセージを受信した場合の処理
    CAN_read(); // CANメッセージの処理
    receive_flag = false; // フラグをリセット
  }

  time_old = time_now;
  time_now = micros();
  dt = (time_now - time_old) * 1e-6f;

  // motor.loopFOC();
  // sensor.update();

  kalman.update(sensor.getAngle()/gear_rate, dt);

  float omega = kalman.getOmega();
  float alpha = kalman.getAlpha();

  leg_angle = (sensor.getAngle() - sensor_offset) / gear_rate;

  if(is_moving){
    if(control_mode == ANGLEMODE){
      torque_est = Disturbance_OB(motor.current.q*KT*gear_rate, alpha, omega, leg_angle);
      control_torque = PID_position(control_cash, leg_angle, omega, dt);

      target_torque = (control_torque + torque_est) / (KT * gear_rate);
      // if(target_torque > torque_limit/gear_rate/KT) target_torque = torque_limit/gear_rate/KT;
      // if(target_torque < -torque_limit/gear_rate/KT) target_torque = -torque_limit/gear_rate/KT;
      if(target_torque > current_limit) target_torque = current_limit;
      if(target_torque < -current_limit) target_torque = -current_limit;
      motor.target = target_torque;

      // t_count++;
      // if(t_count > 10){
      //   t_count = 0;
      //   Serial.printf("P:%f %f\n",target_torque,angle);
      // }
    }else if(control_mode == VELOCITYMODE){
      // control_torque = PID_velocity(control_cash, omega, dt);

      // target_torque = control_torque / KT / gear_rate;
      // motor.target = target_torque;
      // Serial.printf("S:%d %f\n",control_torque, dt);
    }
    if(leg_angle > angle_limit){
      torque_est = Disturbance_OB(target_torque*KT*gear_rate, alpha, omega, leg_angle);
      control_torque = PID_position(angle_limit-0.01, leg_angle, omega, dt);

      target_torque = (control_torque + torque_est) / (KT * gear_rate);
      if(target_torque > 2.4) target_torque = 2.4;
      if(target_torque < -2.4) target_torque = -2.4;
      motor.target = target_torque;
    }else if(leg_angle < -angle_limit){
      torque_est = Disturbance_OB(target_torque*KT*gear_rate, alpha, omega, leg_angle);
      control_torque = PID_position(-angle_limit+0.01, leg_angle, omega, dt);

      target_torque = (control_torque + torque_est) / (KT * gear_rate);
      if(target_torque > 2.4) target_torque = 2.4;
      if(target_torque < -2.4) target_torque = -2.4;
      motor.target = target_torque;
    }
  }

  // motor.move(target_torque);
}

void SimpleFOC_setup() {
  // デバッグ出力を行う
  SimpleFOCDebug::enable(&Serial);
  
  // センサーの初期化
  sensor.init();
  // モータとセンサーをリンク
  motor.linkSensor(&sensor);
  // set calibration values
  motor.zero_electric_angle  = zero_angle; // rad
  motor.sensor_direction = Direction::CW; // CW or CCW

  // pwm frequency to be used [Hz]
  driver.pwm_frequency = 20000;
  // power supply voltage [V]
  driver.voltage_power_supply = INPUT_VOLTAGE;
  // Max DC voltage allowed - default voltage_power_supply
  driver.enable_pin = 21; // nSLEEP pin
  driver.enable_active_high = true; // enable pin is active high
  driver.dead_zone = 0.02; // dead time for the pwm signal [0,1] - 2% of the pwm cycle
  // driver init
  driver.init();
  // link driver
  motor.linkDriver(&driver);

  // init current sense
  current_sense.init();
  // link the driver with the current sense
  current_sense.linkDriver(&driver);

  // velocity loop PID
  motor.PID_velocity.P = 0.1;
  motor.PID_velocity.I = 0.1;
  motor.PID_velocity.D = 0.001;
  motor.PID_velocity.output_ramp = 10.0;
  motor.PID_velocity.limit = 0.5;
  // Low pass filtering time constant 
  motor.LPF_velocity.Tf = 0.05;
  // angle loop PID
  motor.P_angle.P = 20.0;
  motor.P_angle.I = 0.0;
  motor.P_angle.D = 0.0;
  motor.P_angle.output_ramp = 0.0;
  motor.P_angle.limit = 70.0;
  // Low pass filtering time constant 
  motor.LPF_angle.Tf = 0.0;
  // current q loop PID 
  motor.PID_current_q.P = 30.0; //30.0
  motor.PID_current_q.I = 100.0;  //100.0
  motor.PID_current_q.D = 0.0;
  motor.PID_current_q.output_ramp = 0.0; // 0.0
  motor.PID_current_q.limit = 12.0;
  // Low pass filtering time constant 
  motor.LPF_current_q.Tf = 0.05;
  // current d loop PID
  motor.PID_current_d.P = 30.0;
  motor.PID_current_d.I = 100.0;
  motor.PID_current_d.D = 0.0;
  motor.PID_current_d.output_ramp = 0.0;
  motor.PID_current_d.limit = 12.0;
  // Low pass filtering time constant 
  motor.LPF_current_d.Tf = 0.05;
  // Limits 
  motor.velocity_limit = 70.0;
  motor.voltage_limit = 12.0;
  motor.current_limit = 0.81;

  // choose FOC modulation
  motor.foc_modulation = FOCModulationType::SpaceVectorPWM;

  // set motion control loop to be used
  motor.torque_controller = TorqueControlType::foc_current;
  motor.controller = MotionControlType::torque;

  // comment out if not needed
  motor.useMonitoring(Serial);

  // initialize motor
  motor.init();

  // init current sense
  current_sense.init();
  // link the current sense to the motor
  motor.linkCurrentSense(&current_sense);
  // invert phase b gain
  #if (LEG == 1)

  #elif (LEG == 4)
    current_sense.gain_a *=-1;
    current_sense.gain_b *=-1;
    current_sense.gain_c *=-1;
  #else
    current_sense.gain_a *=-1;
    current_sense.gain_b *=-1;
  #endif
  //current_sense.gain_c *=-1;
  // skip alignment
  current_sense.skip_align = true;

  // start the FOC
  motor.initFOC();

  // add target command M
  //command.add('M', doMotor, "Motor");
  // tell the motor to use the monitoring
  //motor.useMonitoring(Serial);
  //motor.monitor_downsample = 0; // disable monitor at first - optional
}

void focTask(void *pvParameters) {
  while (true) {
    motor.loopFOC();
    //sensor.update();
    
    motor.move();
  }
}

void CAN_read() {
  //if (receive_id == CAN_MASK){
    switch(receive_CANdata[0]){
      case 'A': // モーターの角度を取得
        //sensor.update();
        current_cash = current_sense.getDCCurrent();
        // send_CANdata[0] = 'A';
        // ((float*)&send_CANdata[1])[0] = sens_cash; // 1バイト目以降にfloatをコピー
        // send_length = 1 + sizeof(float); // 5
        ((float*)&send_CANdata[0])[0] = leg_angle; // 0バイト目以降にfloatをコピー
        ((float*)&send_CANdata[4])[0] = current_cash; // 4バイト目以降にfloatをコピー
        send_length = sizeof(float) + sizeof(float); // 8
        send_flag = true; // 送信フラグを立てる
        break;
      case 'V': // モーターの速度を取得
        //sensor.update();
        sens_cash = sensor.getVelocity();
        current_cash = current_sense.getDCCurrent();
        // send_CANdata[0] = 'V';
        // ((float*)&send_CANdata[1])[0] = sens_cash; // 1バイト目以降にfloatをコピー
        // send_length = 1 + sizeof(float); // 5
        ((float*)&send_CANdata[0])[0] = sens_cash; // 0バイト目以降にfloatをコピー
        ((float*)&send_CANdata[4])[0] = current_cash; // 4バイト目以降にfloatをコピー
        send_length = sizeof(float) + sizeof(float); // 8
        send_flag = true; // 送信フラグを立てる
        break;
      case 'C': // モーターの電流を取得
        break;
      case 'T': // モーターのトルクを指定
        if(control_mode != TORQUEMODE) control_mode = TORQUEMODE;
        control_cash = *((float*)&receive_CANdata[1]); // 1バイト目以降をfloatとして取得
        motor.target = control_cash; // 目標トルクを設定

        //current_sense.update();
        current_cash = current_sense.getDCCurrent(); // 電流を取得
        // send_CANdata[0] = 'A'; // 角度取得のコマンド
        // ((float*)&send_CANdata[1])[0] = sens_cash; // 1バイト目以降に角度をfloatとしてコピー
        // send_length = 1 + sizeof(float); // 5
        ((float*)&send_CANdata[0])[0] = leg_angle; // 0バイト目以降にfloatをコピー
        ((float*)&send_CANdata[4])[0] = current_cash; // 4バイト目以降にfloatをコピー
        send_length = sizeof(float) + sizeof(float); // 8
        send_flag = true; // 送信フラグを立てる
        // if(receive_length == 6){
        //   if(receive_CANdata[5] == 'A'){
        //     sensor.update();
        //     sens_cash = sensor.getAngle(); // 角度を取得
        //     current_cash = current_sense.getDCCurrent(); // 電流を取得
        //     // send_CANdata[0] = 'A'; // 角度取得のコマンド
        //     // ((float*)&send_CANdata[1])[0] = sens_cash; // 1バイト目以降に角度をfloatとしてコピー
        //     // send_length = 1 + sizeof(float); // 5
        //     ((float*)&send_CANdata[0])[0] = sens_cash; // 0バイト目以降にfloatをコピー
        //     ((float*)&send_CANdata[4])[0] = current_cash; // 4バイト目以降にfloatをコピー
        //     send_length = sizeof(float) + sizeof(float); // 8
        //     send_flag = true; // 送信フラグを立てる
        //   }else if(receive_CANdata[5] == 'V'){
        //     sensor.update();
        //     sens_cash = sensor.getVelocity(); // 速度を取得
        //     current_cash = current_sense.getDCCurrent(); // 電流を取得
        //     // send_CANdata[0] = 'V'; // 速度取得のコマンド
        //     // ((float*)&send_CANdata[1])[0] = sens_cash; // 1バイト目以降に速度をfloatとしてコピー
        //     // send_length = 1 + sizeof(float); // 5
        //     ((float*)&send_CANdata[0])[0] = sens_cash; // 0バイト目以降にfloatをコピー
        //     ((float*)&send_CANdata[4])[0] = current_cash; // 4バイト目以降にfloatをコピー
        //     send_length = sizeof(float) + sizeof(float); // 8
        //     send_flag = true; // 送信フラグを立てる
        //   }
        // }
        break;
      case 'S': // モーターの速度を指定
        if(control_mode == VELOCITYMODE){
          control_cash = *((float*)&receive_CANdata[1]); // 1バイト目以降をfloatとして取得
          motor.target = control_cash; // 目標速度を設定

          //current_sense.update();
          current_cash = current_sense.getDCCurrent(); // 電流を取得
          // send_CANdata[0] = 'A'; // 角度取得のコマンド
          // ((float*)&send_CANdata[1])[0] = sens_cash; // 1バイト目以降に角度をfloatとしてコピー
          // send_length = 1 + sizeof(float); // 5
          ((float*)&send_CANdata[0])[0] = leg_angle; // 0バイト目以降にfloatをコピー
          ((float*)&send_CANdata[4])[0] = current_cash; // 4バイト目以降にfloatをコピー
          send_length = sizeof(float) + sizeof(float); // 8
          send_flag = true; // 送信フラグを立てる
        }else if(control_mode == ANGLEMODE){
          //control_cash = *((float*)&receive_CANdata[1]); // 1バイト目以降をfloatとして取得
          //motor.velocity_limit = control_cash; // 速度制限を設定
        }
        // if(receive_length == 6){
        //   if(receive_CANdata[5] == 'A'){
        //     sensor.update();
        //     sens_cash = sensor.getAngle(); // 角度を取得
        //     current_cash = current_sense.getDCCurrent(); // 電流を取得
        //     // send_CANdata[0] = 'A'; // 角度取得のコマンド
        //     // ((float*)&send_CANdata[1])[0] = sens_cash; // 1バイト目以降に角度をfloatとしてコピー
        //     // send_length = 1 + sizeof(float); // 5
        //     ((float*)&send_CANdata[0])[0] = sens_cash; // 0バイト目以降にfloatをコピー
        //     ((float*)&send_CANdata[4])[0] = current_cash; // 4バイト目以降にfloatをコピー
        //     send_length = sizeof(float) + sizeof(float); // 8
        //     send_flag = true; // 送信フラグを立てる
        //   }else if(receive_CANdata[5] == 'V'){
        //     sensor.update();
        //     sens_cash = sensor.getVelocity(); // 速度を取得
        //     current_cash = current_sense.getDCCurrent(); // 電流を取得
        //     // send_CANdata[0] = 'V'; // 速度取得のコマンド
        //     // ((float*)&send_CANdata[1])[0] = sens_cash; // 1バイト目以降に速度をfloatとしてコピー
        //     // send_length = 1 + sizeof(float); // 5
        //     ((float*)&send_CANdata[0])[0] = sens_cash; // 0バイト目以降にfloatをコピー
        //     ((float*)&send_CANdata[4])[0] = current_cash; // 4バイト目以降にfloatをコピー
        //     send_length = sizeof(float) + sizeof(float); // 8
        //     send_flag = true; // 送信フラグを立てる
        //   }
        // }
        break;
      case 'P': // モーターの位置を指定
        if(control_mode != ANGLEMODE) control_mode = ANGLEMODE;
        control_cash = *((float*)&receive_CANdata[1]); // 1バイト目以降をfloatとして取得
        //motor.target = control_cash; // 目標角度を設定

        //current_sense.update();
        current_cash = current_sense.getDCCurrent(); // 電流を取得
        // send_CANdata[0] = 'A'; // 角度取得のコマンド
        // ((float*)&send_CANdata[1])[0] = sens_cash; // 1バイト目以降に角度をfloatとしてコピー
        // send_length = 1 + sizeof(float); // 5
        ((float*)&send_CANdata[0])[0] = leg_angle; // 0バイト目以降にfloatをコピー
        ((float*)&send_CANdata[4])[0] = current_cash; // 4バイト目以降にfloatをコピー
        send_length = sizeof(float) + sizeof(float); // 8
        send_flag = true; // 送信フラグを立てる
        // if(receive_length == 6){
        //   if(receive_CANdata[5] == 'A'){
        //     sensor.update();
        //     sens_cash = sensor.getAngle(); // 角度を取得
        //     current_cash = current_sense.getDCCurrent(); // 電流を取得
        //     // send_CANdata[0] = 'A'; // 角度取得のコマンド
        //     // ((float*)&send_CANdata[1])[0] = sens_cash; // 1バイト目以降に角度をfloatとしてコピー
        //     // send_length = 1 + sizeof(float); // 5
        //     ((float*)&send_CANdata[0])[0] = sens_cash; // 0バイト目以降にfloatをコピー
        //     ((float*)&send_CANdata[4])[0] = current_cash; // 4バイト目以降にfloatをコピー
        //     send_length = sizeof(float) + sizeof(float); // 8
        //     send_flag = true; // 送信フラグを立てる
        //   }else if(receive_CANdata[5] == 'V'){
        //     sensor.update();
        //     sens_cash = sensor.getVelocity(); // 速度を取得
        //     current_cash = current_sense.getDCCurrent(); // 電流を取得
        //     // send_CANdata[0] = 'V'; // 速度取得のコマンド
        //     // ((float*)&send_CANdata[1])[0] = sens_cash; // 1バイト目以降に速度をfloatとしてコピー
        //     // send_length = 1 + sizeof(float); // 5
        //     ((float*)&send_CANdata[0])[0] = sens_cash; // 0バイト目以降にfloatをコピー
        //     ((float*)&send_CANdata[4])[0] = current_cash; // 4バイト目以降にfloatをコピー
        //     send_length = sizeof(float) + sizeof(float); // 8
        //     send_flag = true; // 送信フラグを立てる
        //   }
        //}
        break;
      case 'E': // モーターのONOFF
        if(receive_CANdata[1] == '1') {
          is_moving = true;
          digitalWrite(state_Pin, HIGH);
          motor.PID_velocity.reset();
          motor.P_angle.reset();
          motor.PID_current_q.reset();
          motor.PID_current_d.reset();
          driver.enable(); // ドライバを有効化
          motor.enable(); // モーターを有効化
        } else if (receive_CANdata[1] == '0') {
          motor.disable(); // モーターを無効化
          driver.disable(); // ドライバを無効化
          is_moving = false;
          digitalWrite(state_Pin, LOW);
          motor.PID_velocity.reset();
          motor.P_angle.reset();
          motor.PID_current_q.reset();
          motor.PID_current_d.reset();
        }
        break;
      case 'L': // モーターのキャリブレーション
        calibration();
        break;
      case 'M': // モーターのモード変更
        motor.disable(); // モーターを一旦停止
        driver.disable(); // ドライバを一旦停止
        if(receive_CANdata[1] == 'P') {
          //motor.controller = MotionControlType::angle;
          motor.controller = MotionControlType::torque;
          control_cash = *((float*)&receive_CANdata[2]);
          //motor.target = control_cash;
          control_mode = ANGLEMODE; // 角度制御モード
        } else if (receive_CANdata[1] == 'S') {
          motor.controller = MotionControlType::velocity;
          control_cash = *((float*)&receive_CANdata[2]);
          motor.target = control_cash;
          control_mode = VELOCITYMODE; // 速度制御モード
        } else if (receive_CANdata[1] == 'T') {
          motor.controller = MotionControlType::torque;
          control_cash = *((float*)&receive_CANdata[2]);
          motor.target = control_cash;
          control_mode = TORQUEMODE; // トルク制御モード
        }
        if(is_moving == true) {
          driver.enable(); // ドライバを再開
          motor.enable(); // モーターを再開
        }
        if(receive_length == 7){
          if(receive_CANdata[6] == 'A'){
            sensor.update();
            sens_cash = sensor.getAngle(); // 角度を取得
            current_cash = current_sense.getDCCurrent(); // 電流を取得
            // send_CANdata[0] = 'A'; // 角度取得のコマンド
            // ((float*)&send_CANdata[1])[0] = sens_cash; // 1バイト目以降に角度をfloatとしてコピー
            // send_length = 1 + sizeof(float); // 5
            ((float*)&send_CANdata[0])[0] = sens_cash; // 0バイト目以降にfloatをコピー
            ((float*)&send_CANdata[4])[0] = current_cash; // 4バイト目以降にfloatをコピー
            send_length = sizeof(float) + sizeof(float); // 8
            send_flag = true; // 送信フラグを立てる
          }else if(receive_CANdata[6] == 'V'){
            sensor.update();
            sens_cash = sensor.getVelocity(); // 速度を取得
            current_cash = current_sense.getDCCurrent(); // 電流を取得
            // send_CANdata[0] = 'V'; // 速度取得のコマンド
            // ((float*)&send_CANdata[1])[0] = sens_cash; // 1バイト目以降に速度をfloatとしてコピー
            // send_length = 1 + sizeof(float); // 5
            ((float*)&send_CANdata[0])[0] = sens_cash; // 0バイト目以降にfloatをコピー
            ((float*)&send_CANdata[4])[0] = current_cash; // 4バイト目以降にfloatをコピー
            send_length = sizeof(float) + sizeof(float); // 8
            send_flag = true; // 送信フラグを立てる
          }
        }
        break;
      case 'B': // リミット設定
        if(receive_CANdata[1] == 'T'){ // トルク(電流)リミット設定
          motor.current_limit = *((float*)&receive_CANdata[2]);
          current_limit = *((float*)&receive_CANdata[2]);
        }else if(receive_CANdata[1] == 'V'){ // 速度リミット設定
          
        }else if(receive_CANdata[1] == 'A'){ // 角度リミット設定
          angle_limit = radians(*((float*)&receive_CANdata[2]));
        }
        break;
      case 'R': // 基板のリセット
        ESP.restart();
        break;
      default:
        break;
    }
  //}
}
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

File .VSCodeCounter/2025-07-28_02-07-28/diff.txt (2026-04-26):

Date : 2025-07-28 02:07:28
Directory : e:\OneDrive\vscode\zyudou\simpleFOC_CAN_DOB
Total : 28 files,  -482 codes, 169 comments, -19 blanks, all -332 lines

Languages
+----------+------------+------------+------------+------------+------------+
| language | files      | code       | comment    | blank      | total      |
+----------+------------+------------+------------+------------+------------+
| Markdown |          8 |          9 |          0 |          0 |          9 |
| JSON     |          2 |          0 |          0 |          0 |          0 |
| Ini      |          2 |         -9 |          0 |         -3 |        -12 |
| C++      |         16 |       -482 |        169 |        -16 |       -329 |
+----------+------------+------------+------------+------------+------------+

Directories
+------------------------------------------------------------------------------------------------+------------+------------+------------+------------+------------+
| path                                                                                           | files      | code       | comment    | blank      | total      |
+------------------------------------------------------------------------------------------------+------------+------------+------------+------------+------------+
| .                                                                                              |         28 |       -482 |        169 |        -19 |       -332 |
| . (Files)                                                                                      |          1 |         12 |          9 |          2 |         23 |
| ..                                                                                             |         17 |     -1,201 |        -63 |       -196 |     -1,460 |
| ..\M5-controll                                                                                 |         17 |     -1,201 |        -63 |       -196 |     -1,460 |
| ..\M5-controll (Files)                                                                         |          1 |        -21 |         -9 |         -5 |        -35 |
| ..\M5-controll\.VSCodeCounter                                                                  |          5 |        -60 |          0 |        -26 |        -86 |
| ..\M5-controll\.VSCodeCounter\2025-07-28_02-06-30                                              |          5 |        -60 |          0 |        -26 |        -86 |
| ..\M5-controll\src                                                                             |         11 |     -1,120 |        -54 |       -165 |     -1,339 |
| .VSCodeCounter                                                                                 |          5 |         69 |          0 |         26 |         95 |
| .VSCodeCounter\2025-07-28_02-06-57                                                             |          5 |         69 |          0 |         26 |         95 |
| src                                                                                            |          5 |        638 |        223 |        149 |      1,010 |
+------------------------------------------------------------------------------------------------+------------+------------+------------+------------+------------+
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

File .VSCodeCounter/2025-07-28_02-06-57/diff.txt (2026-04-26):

Date : 2025-07-28 02:06:57
Directory : e:\OneDrive\vscode\zyudou\M5-controll
Total : 0 files,  0 codes, 0 comments, 0 blanks, all 0 lines

Languages
+----------+------------+------------+------------+------------+------------+
| language | files      | code       | comment    | blank      | total      |
+----------+------------+------------+------------+------------+------------+
+----------+------------+------------+------------+------------+------------+

Directories
+------+------------+------------+------------+------------+------------+
| path | files      | code       | comment    | blank      | total      |
+------+------------+------------+------------+------------+------------+
+------+------------+------------+------------+------------+------------+

Files
+----------+----------+------------+------------+------------+------------+
| filename | language | code       | comment    | blank      | total      |
+----------+----------+------------+------------+------------+------------+
| Total    |          |          0 |          0 |          0 |          0 |
+----------+----------+------------+------------+------------+------------+

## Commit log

2026-04-26 モーターコントローラファイル追加
    [diff.csv, diff.txt, results.csv]
2026-04-26 KiCADファイル追加、readme更新
    [bom.csv, designators.csv, drv8311.dsn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]
2026-04-26 redme更新
